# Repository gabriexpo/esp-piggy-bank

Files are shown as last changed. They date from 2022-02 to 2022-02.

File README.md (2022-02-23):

# esp-piggy-bank
Un progetto per implementare un salvadanaio intelligente con alla base un ESP8266.

### Componenti utilizzate

- ESP8266 D1 mini
- Arduino UNO
- Potenziometro
- ULN2003 Stepper Motor Driver Module
- Stepper Motor
- Power Module (Power MB-V2)
- 4 Digit 7-Segment Display (module 5641AS)

### Obbiettivo

L'obbiettivo di questo progetto è quello di creare un salvadanaio intelligente (smart piggy bank) che sia in grado di riconoscere il tipo di moneta inserita e che, una volta riconosciuta la moneta, invii una notifica ad un server mqtt e salvi la situazione corrente del salvadanaio nella memoria EEPROM. Per dare un feedback all'utente che inserisce la moneta è presente anche un display che comunicare l'avvenuto riconoscimento della moneta mostrando il valore della moneta stessa.

### Riconoscimento della moneta

Il riconoscimento della moneta si basa su una leva ancorata ad una estremità che viene fatta ruotare su un perno dal passaggio della moneta. Il movimento rotatorio passa quindi ad alcuni ingranaggio che amplificano il movimento rotatorio prodotto dalla leva e rendono più semplice al potenziometro distinguere le varie monete in base alla grandezza.
Una volta che la moneta riesce a passare tra la leva e la sponda rigida del salvadanaio la moneta viene identificata e la leva viene riposizionata dallo stepper motor che agisce sugli ingranaggi sottostanti alla leva.

### Schema


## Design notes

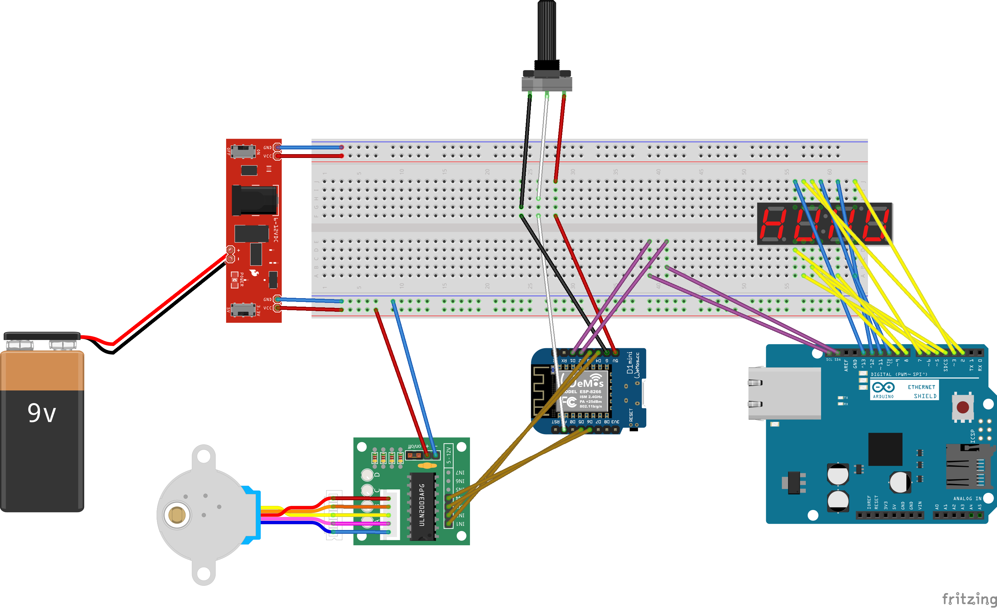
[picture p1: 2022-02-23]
scheme.png

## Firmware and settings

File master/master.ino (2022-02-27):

#include <Stepper.h>
#include <Wire.h>
#include <ESP_EEPROM.h>
#include <EspMQTTClient.h>
#include "costanti.h"

// EspMQTTClient init

EspMQTTClient client(
  WIFI,             // da costanti.h
  PASSWORD,         // da costanti.h
  "192.168.1.54",  // MQTT Broker server ip
//  "MQTTUsername",   // Omesso dato che uso una connessione anonima
//  "MQTTPassword",   // Omesso dato che uso una connessione anonima
  "ESP8266",        // Client name
  1883              // The MQTT port, default to 1883. this line can be omitted
);

// Stepper init

const int steps_per_revolution = 2048;
Stepper *myStepper = new Stepper(steps_per_revolution, D6, D4, D5, D3);

// I2C data

#define SDA_PIN D2
#define SCL_PIN D1
const int16_t I2C_MASTER = 0x42;
const int16_t I2C_SLAVE = 0x08;


// Soglie per il riconoscimento delle monete

/*  Alcune delle misurazioni (n/m -> valore che oscilla tra n e m)
  Moneta -> [misurazioni]
  
  10  -> 194/195 - 195 - 195/196 - 195/196
  20  -> 217/218 - 216 - 214 - 214
  50  -> 229/230 - 229/230 - 229
  1   -> 221/222 - 220/221 - 223 - 222 - 220
  2   -> 241/242 - 241 - 238 - 238/240 - 240/241
*/

#define MIN10c 190
#define MAX10c 197
#define MIN20c 213
#define MAX20c 218
#define MIN1e 219
#define MAX1e 224
#define MIN50c 228
#define MAX50c 231
#define MIN2e 236
#define MAX2e 249

int baseValue = 0;
int sensorValue = 0;

float total;

// -----
// SETUP
// -----

void setup() {
  Serial.begin(115200);
  
  // Set Stepper motor speed
  myStepper->setSpeed(5);

  // Setting up EEPROM memory space and retrieving total
  EEPROM.begin(16);
  EEPROM.get(0, total);

  // Setting up i2c connection
  Wire.begin(SDA_PIN, SCL_PIN, I2C_MASTER);

  // Setting MQTT related options
  client.enableDebuggingMessages();
  client.enableMQTTPersistence();
  //client.enableLastWillMessage("ESP8266/piggy-bank", "Piggy-bank going offline!");

  // Setting up base value for measurement
  setBaseValue();
}

// ----
// LOOP
// ----

void loop() {

  client.loop();
  
  int currSensorValue = analogRead(A0);
  if (abs(currSensorValue - baseValue) > 20) {        // 20 valore fissato per indicare un cambiamento significativo nello stato del potenziometro
    Serial.println(currSensorValue);
    
    measurement();
    String coin = getCoin();
    Serial.println(coin);
    
    // update total
    if (coin != "nan") {
      total += coin.toFloat();
      //Serial.println(coin.toFloat());
      Serial.print("Total: ");
      Serial.println(total);

      // EEPROM
      EEPROM.put(0, total);
      boolean res = EEPROM.commit();
      Serial.println((res) ? "Commit ok" : "Commit failed");

      // send to mqtt
      client.publish("ESP8266/piggy-bank", "Inserted coin: " + coin);
    }
    
    // send to slave
    i2c_Transmission(coin);

    delay(500);
    // reposition lever
    repositionLever();
    Serial.println("Fine");
  }

  delay(1000);
  
}

void onConnectionEstablished() {
  // Subscribe to ESP8266/piggy-bank to check messages arrived to MQTT server
  client.subscribe("ESP8266/piggy-bank", [](const String & payload) {
    Serial.println("MQTT server received: " + payload);
  });
  
  client.publish("ESP8266/piggy-bank", "Piggy-bank online!");
}

// Funzione per stabilire il valore "a riposo" che percepisce il potenziometro.

void setBaseValue() {
  int sum = 0;
  int current = 0;
  
  for(int i = 0; i < 10; i++) {   // prime read per togliere dei risultati strani
    delay(100);
    current = analogRead(A0);
    //Serial.println(current);
  }
  
  for(int i = 0; i < 10; i++) {   // read per calcolare il valore base
    delay(100);
    current = analogRead(A0);
    //Serial.println(current);
    sum += current;
  }
  
  baseValue = sum / 10;
  sensorValue = baseValue;
  
  Serial.println("Base value:");
  Serial.println(baseValue);
}

// Funzione per trasmettere, sotto forma di stringa, il valore della moneta
// inserita alla board slave.

void i2c_Transmission(String message) {
  Wire.beginTransmission(I2C_SLAVE);  // transmit to slave
  Wire.write(message.c_str());
  Wire.endTransmission();    // stop transmitting
}

// Funzione che aspetta che l'utente finisca di far passare la moneta
// tra la barra di misurazione e la parete di sostegno e che termina 
// ponendo SensorValue al valore raggiunto dal passaggio della moneta.

void measurement() {
  Serial.println("Measurement:");

  int diff;
  
  do {
    delay(200);             // forse gioco un po' con il delay
    int currSensorValue = analogRead(A0);
    diff = abs(sensorValue - currSensorValue);
    sensorValue = currSensorValue;
    //Serial.println(sensorValue);
  } while(diff > 3);
  
}

// Funzione che trasforma il valore del potenziometro (nella variabile sensorValue)
// in una stringa contenente il valore della moneta secondo le soglie definite 
// nelle prime righe del codice

String getCoin() {
  String coin;
  
  if (sensorValue >= MIN10c && sensorValue <= MAX10c) {
    coin = "0.10";
  } else if (sensorValue >= MIN20c && sensorValue <= MAX20c) {
    coin = "0.20";
  } else if (sensorValue >= MIN1e && sensorValue <= MAX1e) {
    coin = "1.00";
  } else if (sensorValue >= MIN50c && sensorValue <= MAX50c) {
    coin = "0.50";
  } else if (sensorValue >= MIN2e && sensorValue <= MAX2e) {
    coin = "2.00";
  } else {
    coin = "nan";
  }

  return coin;
}

// Funzione per riposizionare la leva che aziona il potenziometro dopo una misurazione

void repositionLever() {
  Serial.println("Reposition lever:");
  
  int stepsTaken = 0;
  int current;
  
  while (abs(sensorValue - baseValue) > 2) {
    myStepper->step(-2);
    stepsTaken += 2;
    current = analogRead(A0);
    sensorValue = current;
    //Serial.println(current);
    delay(1);
  }

  //myStepper->step(-500); errore se provo con step troppo grandi

  for (int i = 0; i < stepsTaken / 2; i++) {
    myStepper->step(2);
    delay(1);
  }
}

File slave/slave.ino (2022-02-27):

#include <Wire.h>
#include <Simple5641AS.h>

#define T 15

// 5641AS stuff

const uint8_t segmentPins[] = {2, 3, 4, 5, 6, 7, 8, 9};
const uint8_t digitSelectionPins[] = {10, 11, 12, 13};

Simple5641AS component(segmentPins, digitSelectionPins);

// Setup

void setup() {
  Wire.begin(8);                // join i2c bus with address #8
  Wire.onReceive(receiveEvent);
  Serial.begin(115200);
}

// Loop

void loop() {
  delay(1000);
}

// Functions

void receiveEvent(size_t howMany) {
  String data = "";
  while (Wire.available() > 0) {
    data += (char) Wire.read();
  }
  Serial.println(data);

  // Chiamata alla funzione di display della moneta
  displayCoin(data);
}

// Funzione per fare il display della moneta

void displayCoin(String c) {
  uint8_t x[] = {B00000000, B00000000, B00000000, B00000000};

  if (c == "0.10") {
    //x = [B11111100, B11111101, B01100000, B11111100];   // 00.10
    x[0] = 252;   // 00.10
    x[1] = 253;
    x[2] = 96;
    x[3] = 252;
  } else if (c == "0.20") {
    //x = [B11111100, B11111101, B11011010, B11111100];   // 00.20
    x[0] = 252;   // 00.20
    x[1] = 253;
    x[2] = 218;
    x[3] = 252;
  } else if (c == "0.50") {
    //x = [B11111100, B11111101, B10110110, B11111100];   // 00.50
    x[0] = 252;   // 00.50
    x[1] = 253;
    x[2] = 182;
    x[3] = 252;
  } else if (c == "1.00") {
    //x = [B11111100, B01100001, B11111100, B11111100];   // 01.00
    x[0] = 252;   // 01.00
    x[1] = 97;
    x[2] = 252;
    x[3] = 252;
  } else if (c == "2.00") {
    //x = [B11111100, B11011011, B11111100, B11111100];   // 02.00
    x[0] = 252;   // 02.00
    x[1] = 219;
    x[2] = 252;
    x[3] = 252;
  } else {
    x[0] = 158;   // EEEE (Errore)
    x[1] = 158;
    x[2] = 158;
    x[3] = 158; 
  }

  component.displayCode(T, x, 0);
}

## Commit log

2022-02-21 Aggiunta la connessione con lo slave via I2C
2022-02-23 Aggiunto schema fritzing e aggiornamento readme
    [scheme.fzz]
2022-02-27 Fix per mqtt connection e per il cast dei float (per salvare su EEPROM)
    [master.ino, slave.ino]
